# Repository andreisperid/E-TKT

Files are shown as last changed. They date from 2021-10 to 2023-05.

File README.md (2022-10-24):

teaser_4

<br>

<a href="https://certification.oshwa.org/br000010.html" target="_blank">
  <picture>
    <source media="(prefers-color-scheme: dark)" srcset="https://user-images.githubusercontent.com/15098003/196943625-ccef0886-9a68-493c-814a-6e63b238b2bd.png">
    <source media="(prefers-color-scheme: light)" srcset="https://user-images.githubusercontent.com/15098003/196943559-973e30a0-acfd-4a96-a7b8-da4f9bf773d8.png">
    
  </picture>
</a>

<br>

<h1 align="center">E-TKT: anachronic label maker</h1>
<h5 align="center">Andrei Speridião - 2022 - <a href="https://andrei.cc">andrei.cc</a></h6>

<br>

<h3 align="center"><i>An open source label maker that fuses together both old and contemporary technology to create something as ubiquitous as... EMBOSSED LABELS!</i></h2>

<br>

By combining simple and widely available embossing tapes in a reliable mechanism with modern connectivity, E-TKT rescues a *would-be future* that did not happen, and at the same time *gets rid of the dependence on proprietary cartridges*, which are environmentally impacting & expensive.

<br>
<br>

_DSC0933

<br>



<br><br>

# how does it work?

<picture>
  <source media="(prefers-color-scheme: dark)" srcset="https://user-images.githubusercontent.com/15098003/196457261-b6343e3f-528d-4cbe-a548-1b4f4463e4a1.png">
  <source media="(prefers-color-scheme: light)" srcset="https://user-images.githubusercontent.com/15098003/196947337-6aefe414-159e-483b-9dc4-a49cfc82c548.png">
  
</picture>

An *ESP32* commands the label production and also serves an on demand web application (local) to any device connected in a local network.

***Neither internet is needed, nor installing any app.***

<br>

# documentation 

It's now much more detailed, so I've moved it to a [dedicated page](https://andreisperid.github.io/E-TKT/).

### What you fill find there:

- [🎯 news](https://andreisperid.github.io/E-TKT/news.html): what's going on;
- [🤓 about](https://andreisperid.github.io/E-TKT/about.html): how it started, and why?
- [⚙️ how does it work?](https://andreisperid.github.io/E-TKT/how.html): a more in depth explanation;
- [💡 features](https://andreisperid.github.io/E-TKT/features.html): device and app details;
- [📷 gallery](https://andreisperid.github.io/E-TKT/gallery.html): misc. photos of the device and labeled things;
- [🛠️ do it yourself](https://andreisperid.github.io/E-TKT/diy/diy.html): a **super** detailed guide for you to buy the parts and make your own E-TKT;
- [🧬 iterations](https://andreisperid.github.io/E-TKT/iterations/iterations.html): a log of development so far;
- [⚖️ license](https://andreisperid.github.io/E-TKT/license.html): for firmware, hardware and documentation itself;
- [🏅 credits](https://andreisperid.github.io/E-TKT/credits/credits.html): people that made a difference for the project;
- [📺 media](https://andreisperid.github.io/E-TKT/media.html): where and when it's already been featured.

<br>

### If you ever build one, [I would love to know](mailto:hi@andrei.cc) ;)

### And if you'd like, [donations](https://www.paypal.com/donate/?business=U5QYSBT2TLZL8&no_recurring=0&currency_code=USD) are more than welcome 😍

<br>

### *...for other projects: [andrei.cc](https://andrei.cc)*

<br>

_DSC0816

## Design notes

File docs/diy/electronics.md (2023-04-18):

---
layout: default
title: ⚡ electronics
nav_order: 3
description: "E-TKT"
parent: 🛠️ do it yourself!
---

# ⚡ **electronics**

----

💬 *you can find the KiCad v6 source files, PCB 3D export, PDF schematics and gerbers in the [electronic](https://github.com/andreisperid/E-TKT/tree/main/_electronic/) folder.*

----

_DSC0364

----

## Board


----

## Schematics
  
<p align="right">
  <a href="https://github.com/andreisperid/E-TKT/blob/main/_electronic/export/etkt_schematic.pdf" target="_blank">
    <i>🔎 see larger</i>
  </a>
</p>  

----

## Specs
- ***Size:*** 99.6 x 76.2mm(3.92 x 3.00 inches)
- ***Layer count:*** 4
- ***Material:*** FR-4
- ***FR4-TG:*** TG 150-160
- ***Thickness:*** 1.6mm
- ***Min. Track/Spacing:*** 6/6mil
- ***Min. Hole Size:*** 0.3mm↑
- ***Solder Mask:*** Black
- ***Silkscreen:*** White
- ***Surface Finish:*** HASL
- ***Thickness:*** 1.6mm

----

## Subsystems

### Power
  - ***12V*** needs to be provided by an external power supply with at least 3A (real) to deal with servo peaks current while pressing the label. It supplies both the stepper drivers directly.
  - ***6V*** out of the bucket converter and is provided for both the servo and hall sensor. The peak voltage tested on oscilloscope was +1V surge when the servo stalls. *
  - ***3.3V*** is provided by the AZ1117 linear regulator, which receives power directly from the 6V rail.

***Important: Logic level MOSFETs (BSS138)*** were implemented because the ESP32 uses 3.3v logic, we need this conversion for parts that are running on 6V (servo and hall sensor).

<h6><i>* Using a bucket converter for the 6V rail is preferred due to the high step from 12V, but a cheaper alternative using a L7806 (1.5A) is oferred at the PCB back side. For that, you should not mount the bucket converter components (C_POW_IN_1, C_POW_IN_2, C_POW_IN_3, U_POW1, C_POW_BST_1, L1, C_POW_6V_FF1, R_POW_FBT1, R_POW_FFB1, C_POW_OUT_1, C_POW_OUT_2, C_POW_OUT_3, C_POW_OUT_4, C_POW_OUT_5). But IMPORTANT, this exact setup wasn't tested on this exact PCB (only in the preliminar prototype), so do it at your own risk.</i></h6>

### Processing & wireless communication
- Using an ESP32-WROOM-32D-N4, with an integrated antenna.

### Serial USB communication
- An FT231XS-R is used for flashing the firmware through an USB-C 2.0 port.

### Label press
- The MG996-R servo has a maximum constant voltage of 6V. Constant higher tension tends to damage it.

### Character selection (daisy wheel)
- A NEMA stepper driven by a A4988 breakout and a KY 003 hall sensor for homing the daisy wheel.

### Wifi reset
- When this tactile button is pressed while booting the saved wifi credentials are cleared.

### Feeder
- 12v reduced stepper motor (28BYJ-48) driven by a ULN2003 darlington array.

### Graphic user interface
- Running on 3.3v, an I²C OLED display and two DIP LEDs mounted into the J_top piece.

### Buzzer
- Optional magnetic buzzer that plays notes for audible feedback.

----

## Stackup
<p align="center">  

</p>

- **Front (F.Cu)**: most components + mixed signals & power + ground plane;
- **Inner 1 (In1.Cu)**: ground plane;
- **Inner 2 (In2.Cu)**: 6V plane;
- **Back (B.Cu)**: few components + headers + mixed signals and power + ground plane.

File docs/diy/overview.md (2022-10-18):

---
layout: default
title: 🗺️ overview & tips
nav_order: 1
description: "E-TKT"
parent: 🛠️ do it yourself!
---

# 🗺️ **overview & tips**

----

_DSC0414

----

To make your own E-TKT you will need to:
### 1. 3D print
I highly recommend you to have a *3d printer accessible* as you might need to test and tweak the printing settings, since this project demands a certain precision in the fittings;
  
### 2. order a PCB
It's design was oriented to *low cost manufacturing* (4 layers). The two internal layers are ground planes, so it might work with only 2 layers for even lower costs (but it wasn't tested). Don't forget to *order a stencil for the front face* (not needed for the back) together with the PCB.

### 3. buy components
For some electronic parts, you might need to search for alternative *drop-in replacements* (same specs & footprint) as right now there is a general shortage for semiconductors.

### 4. mount the components on the PCB
You can place the components manually in the PCB and then use a home electrical oven/toaster to solder the SMD components. There are PTH headers in the back face and a single SMD electrolytical capacitor that will be easy to deal with a simple soldering station.

### 5. flash the firmware
Very simple process, but please don't forget to *add the data files* together with the firmware.

### 6. assemble the whole package
After making sure the system is working properly, you can proceed to *cable management and physically mounting* the parts together.

### 7. calibrate
The final step makes sure the daisy wheel letters are aligned to the tape and works along with the right pressing force. There is a handy *calibration mode built-in the web app* ;)

<br>

*PS: the PCB order along with the components and it's assembly (steps 2, 3 and 4) might be outsourced by using a turnkey PCB service, but it is funnier to DIY to learn by doing!*

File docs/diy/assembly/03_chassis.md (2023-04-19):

---
layout: default
title: 3. chassis
description: "E-TKT"

parent: 🧩 assembly
grand_parent: 🛠️ do it yourself!
nav_order: 4
---

# **3. chassis**

----

💬 *whenever you need, check out the [exploded view](https://andreisperid.github.io/E-TKT/diy/assembly/assembly.html) for orientation;*

----

This is the foundation of the device. From now on, things will be mounted over it.

_DSC0532

## PCB + NEMA + bottom

_DSC0533
_DSC0534

1. place the PCB and the NEMA assembly together in the A_bottom;
2. pay close attention on the PCB slot on the A_bottom to ease the insertion process;
3. screw 4x m3x20 underneath to attach the NEMA;

## + pillars

_DSC0535
_DSC0536

1. proceeed to use 2x m3x16 screws to hold the pillars, also from the bottom;

## + lateral screws
_DSC0537

1. now, use 3x m3x20 screws from the side to firmly hold the PCB in place

## result
_DSC0538

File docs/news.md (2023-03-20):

---
layout: default
title: 🎯 news
nav_order: 2
description: "E-TKT"
---

# 🎯 **news**

----

### March, 2023
- 🤟 Huge thanks to [Stephen Beechen](https://github.com/sabeechen), who since January has been strongly contributing to the project with great insights and improvements! ([+info](https://github.com/andreisperid/E-TKT/pulls?q=is%3Apr+is%3Aclosed+author%3Asabeechen))

### October, 2022
- Stable PCB, BOM and firmware;
- Documentation with in-depth, step-by-step instructions;

### September, 2022
- ⚠️ A manufactured PCB is being developed and the files are already committed, ***but they are still a work in progress. Aka: not stable and with issues.*** I'm working on that at this moment. Meanwhile, please refer to the [legacy documentation](https://github.com/andreisperid/E-TKT) for reference;

### August, 2022
- E-TKT is a [finalist at the Hackaday Prize 2022, in the Hack it Back category](https://hackaday.com/2022/08/09/2022-hackaday-prize-congratulations-to-the-winners-of-the-hack-it-back-challenge/);
- Huge thanks to [Wesley Lee](https://github.com/wes06) for the assistance on the PCB design and manufacture!

### July, 2022
- Project of the week on [Maker Update #289](https://www.youtube.com/watch?v=3jpaBhROYGc), by [Donald Bell](https://twitter.com/donald);

### June, 2022
- Published the project on [Hackaday](https://hackaday.io/project/185912-e-tkt-anachronic-label-maker)
- E-TKT is now [certified by OSHWA](https://certification.oshwa.org/br000010.html);
- Featured on the front page of [Hackaday](https://hackaday.com/2022/06/15/diy-automated-printer-kerchunks-out-classic-embossed-labels/), [Hackster](https://www.hackster.io/news/e-tkt-prints-embossed-labels-with-the-power-of-iot-5ad25299cf22) and [Make](https://makezine.com/article/maker-news/old-school-label-making-new-school-interface/);

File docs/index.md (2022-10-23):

---
layout: default
title: Home
nav_order: 1
description: "E-TKT"
permalink: /
---
teaser_4

<br>



<h1 align="center">E-TKT: anachronic label maker</h1>

<h6 align="center">Andrei Speridião - 2022 - <a href="https://andrei.cc">andrei.cc</a></h6>

<br>

E-TKT is an open source label maker that fuses together both old and contemporary technology to create something as ubiquitous as... EMBOSSED LABELS!

<br>
<iframe  width="100%" height="500" src="https://www.youtube.com/embed/IKzSupjkA0s" title="YouTube video player" frameborder="0" allow="accelerometer; autoplay; clipboard-write; encrypted-media; gyroscope; picture-in-picture" allowfullscreen></iframe>
<br>

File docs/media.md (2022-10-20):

---
layout: default
title: 📺 media
nav_order: 11
description: "E-TKT"
---

# 📺 **media**

----

### <a href="https://www.youtube.com/watch?v=3jpaBhROYGc" target="_blank">Digi-Key Maker Update</a> (project of the week)
"Ep.289 - Stamp of approval"<br>
*by Donald Bell on June 30, 2022*

----

### <a href="https://makezine.com/article/maker-news/old-school-label-making-new-school-interface/" target="_blank">Make:</a>
"Old School Label Making, New School Interface"<br>
*by Caleb Kraft on June 22, 2022*

----

### <a href="https://www.hackster.io/news/e-tkt-prints-embossed-labels-with-the-power-of-iot-5ad25299cf22" target="_blank">Hacksterio</a>
"E-TKT Prints Embossed Labels with the Power of IoT"<br>
*by Arduino “having11” Guy on June 17, 2022*

----

### <a href="https://hackaday.com/2022/06/15/diy-automated-printer-kerchunks-out-classic-embossed-labels/" target="_blank">Hackaday</a>
"DIY AUTOMATED PRINTER KERCHUNKS OUT CLASSIC EMBOSSED LABELS"<br>
*by Dan Maloney on June 15, 2022*

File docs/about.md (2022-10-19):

---
layout: default
title: 🤓 about
nav_order: 3
description: "E-TKT"
---

# 🤓 **about**

----

## By combining simple and widely available embossing tapes in a reliable mechanism with modern connectivity, E-TKT rescues a ***would-be future that did not happen***, and at the same time reduces the dependence on environmentally impacting DRM-enabled disposable cartridges.

----

## 🧐 **what?**
### *étiquette f (plural étiquettes)*
> ["ticket, memorandum, attach, stick, pierce, sting, to be sharp, goad, puncture, attach, nail"](https://en.wiktionary.org/wiki/%C3%A9tiquette#French)
> 1. tag, label 
> 2. prescribed behavior

It's curious how both meanings are a consequence of each other: we *name things around* to state and reinforce what they are or should be, and at the same time, we end up *influencing our own behaviors* mediated by these labels.

## 🤔 **why?**
### *TLDR: curiosity, technical challenge and of course organizing stuff.*

motex3

The initial spark for this project came from an ordinary manual [labeling device](https://www.aliexpress.com/item/3256801648218535.html) that I bought to organize my workshop. I was ***VERY UPSET*** when I noticed that it was basically rubbish, getting broken and unusable after just a few operations. Just to imagine something made in another part of the world, travelling to me and breaking this way is unbelieavable.

Instead of embossing, it was really embarrassing labels 😅

This little plastic hook (circled in red) grabs a ratchet mechanism (the white plastic part below) to feed the tape forward. I tried to fix and reinforce it, but the failure was unavoidable because there seems to be a critical flaw in the project: it is too weak for the lateral force imposed.

low_DSC8695 copy annotated

At that moment, I could easily buy a brand-new electronic thermal label printer ([such as this Brother model](https://www.brother-usa.com/products/pth110bp)), but something about the vintage embossed finish fascinated me. Also, these new models use expensive DRM [proprietary cartridges](https://www.brother-usa.com/products/tze335) that create a lot of trash after use, not to mention that some other recent models are [DRM protected](https://hackaday.com/2022/03/30/freedmo-gets-rid-of-dymo-label-printer-drm/).

After all, even though the pressing mechanism was poorly made, the daisy wheel was pretty sturdy and sharp-printing. So I thought: can I build over its principles to create a functional device? If so, then why not make it *physical-digital?*

...why bother mixing an archaic printing method with current automation and connectivity features? Because *why not?* It was a technological blind spot ready to be explored!

## 🤯 **reasoning**

### *context & purpose*

1. **CULTURE:** embossed labels are deeply ingrained in culture, as well pointed by [Dan Maloney](https://deadhomersociety.wordpress.com/2015/10/22/quote-of-the-day-2406/) [(*HACKADAY*)](https://hackaday.com/2022/06/15/diy-automated-printer-kerchunks-out-classic-embossed-labels/) and a [spacestationkru](https://best-tv-shows.fandom.com/wiki/Labels_(Dexter%27s_Laboratory)) [(*reddit*)](https://www.reddit.com/r/3Dprinting/comments/vf8acb/comment/icvk1fe/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) and [agent_kater](https://backtothefuture.fandom.com/wiki/Flux_capacitor) [(*reddit*)](https://www.reddit.com/r/3Dprinting/comments/vf8acb/comment/icwgo76/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);
2. **NICHE NEEDS:** there are situations where a paper, flat and/or thermally printed label doesn't fit the needs, let alone the need for the embossed relief;
7. **ERGONOMICS**: when there is no other way than using embossed labels, making them manually is a [straining process](https://www.reddit.com/r/functionalprint/comments/vf8hrq/comment/icvjqvg/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) that might give the operator [repetitive strain injury](https://en.wikipedia.org/wiki/Repetitive_strain_injury);
3. **REACH:** this is a cheap mass-produced device, meaning that lots of [people around the world](https://www.reddit.com/r/coolgithubprojects/comments/vfa2nt/comment/id8e9f5/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) might have one at [home](https://www.reddit.com/r/arduino/comments/vf6rjo/comment/icv9q29/?utm_source=reddit&utm_medium=web2x&context=3) or [work](https://www.reddit.com/r/functionalprint/comments/vf8hrq/comment/icuddop/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);
4. **ENVIRONMENT:** these devices might be already broken: how many kilos of wasted plastic (plus the shipping impact)?
6. **ISSUES:** of course, these folks will be upset and in the end have their needs unaddressed;
8. **ACCESSIBILITY:** [braille labels](https://www.maxiaids.com/reizen-rl-350-braille-labeler) are only a [step of distance](https://www.reddit.com/r/arduino/comments/vf6rjo/comment/icv2cnr/?utm_source=reddit&utm_medium=web2x&context=3) for a possible future [spin off](https://www.reddit.com/r/functionalprint/comments/vf8hrq/comment/icvtlxn/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).

These factors made me think of E-TKT as more than a solution only for myself, but to everyone.

I wanted to create an open source project for a long time and this is why I put a lot of effort into testing all parts extensively and of course crafting this detailed documentation.

## 🤓 **exploration**
###  ...***anachronism***

During the process I've realized that this odd mix between new and old was the biggest underlying curiosity. According to [Wikipedia](https://en.wikipedia.org/wiki/Anachronism):
> “An ***anachronism*** (from the Greek ἀνά ana, 'against' and χρόνος khronos, 'time') is a chronological inconsistency in some arrangements, especially a juxtaposition of people, events, objects, language terms and customs from different time periods”.

The point is: even though the process is digitalized, *the resulting label is totally old school* and there is no easy way of telling if it wasn't made in the traditional way.
  
<br>

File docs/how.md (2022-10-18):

---
layout: default
title: ⚙️ how does it work?
nav_order: 4
description: "E-TKT"
---

# ⚙️ **how does it work?**

----



An *ESP32* commands the label production and also serves an on demand web application (local) to any device connected in a local network.

***Neither internet is needed, nor installing any app.***

### Configuration

The whole process of connecting the E-TKT machine to a local network and then launching the local app is aided by a small ***OLED display*** that provides instructions and a dynamically generated *QR code* with the *URL*, according to the IP attributed by the WLAN.

### Commands

The ***web app*** provides instant text validation, buttons for special characters, a preview of the physical size of the tape, an option to select the desired lateral margins and also real time feedback during the printing process (also present on the device screen). There are specific commands for manually feeding and cutting the tape, and a setup menu where the user can feed a new tape reel and calibrate the machine by adjust the letters alignment and pressure force applied to the daisy wheel.

### Embossing

The label production itself uses the same mechanical principles as the original machine, but is now ***reliable and automated***. A stepper motor feeds the tape while another selects the appropriate character on the daisy wheel according to a home position acquired by a hall sensor. Then a servo motor imprints each character by pressing it's daisy wheel tooth against the tape. That happens successively until the end of the desired label content, when there is a special character position to cut it off. A light blinks to ask for the label to be picked.

----

## Functional block diagram

<br>

<p align="right">
  <a href ="https://user-images.githubusercontent.com/15098003/196293832-6121e267-ee89-4fe7-bddf-c8d8f6bf96c8.png" target="_blank">
    <i>🔎 see larger</i>
  </a>
</p>

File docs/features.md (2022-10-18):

---
layout: default
title: 💡 features
nav_order: 5
description: "E-TKT"
---

# 💡 **features**

----

## 🌟 *highlights*
- No need for internet, app installation, data cables or drivers;
- Command it from any device that is connected to a local network and has a web browser: desktop, tablet, smartphone;
- Compatible with ubiquitous, DRM-less and cheap 9mm generic tape (DYMO-compatible);



## 📱 web app (local)

- Instant preview simulation: what you see is what you get;
- Dynamic check for character validity;
- Estimate of the resulting label dimensions;
- Automatic text centering;
- Margin modes: tight, margin (1 space on each side) or full (maximum input length);
- Buttons for special characters: ♡  ☆  ♪  $ @
- "+ REEL" function to install a new tape reel;
- Manual commands: feed & cut;
- Calibration setup for fine tuning the character alignment and pressing force.

<br>

## 🔌 device

- Full label embossing & cutting;
- Speed: 10 characters per minute;
- Minimum label size to be pickable from the device;
- OLED screen + LED feedback;
- QR code & URL for easily accessing the web app;
- Real time embossing progress;
- Instructions for configuring the wifi;
- Button for clearing the wifi configuration;
- Sound signature: each label owns a subtle melody 🐰🥚

<br>

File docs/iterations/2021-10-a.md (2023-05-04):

---
layout: default
title: 21oct - consist. & usability
nav_order: 96
description: "E-TKT"
parent: 🧬 iterations
---

# **consistency and usability** / Sept-Oct, 2021

----

  

- More compact device, with smaller stepper motor for the daisy wheel.
- Tested using NFC to open web app on smartphone, failed (security standards?).
- OLED display to help on configuration and feedback.
- QR code as an alternative to quickly open web app.
- Improvements on web app usability and visuals.

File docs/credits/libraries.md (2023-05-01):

---
layout: default
title: 📚 libraries
nav_order: 1
description: "E-TKT"
parent: 🏅 credits
---

# 📚 **libraries**

----

### Framework
- Arduino

### Environment
- NODEMCU-32s @3.3.2

### Libraries
- [waspinator/AccelStepper@1.61](https://github.com/waspinator/AccelStepper )
- [madhephaestus/ESP32Servo@0.9.0](https://github.com/madhephaestus/ESP32Servo )
- [ottowinter/ESPAsyncWebServer-esphome@3.0.0](https://github.com/me-no-dev/ESPAsyncWebServer)
- [alanswx/ESPAsyncWiFiManager@0.24](https://github.com/alanswx/ESPAsyncWiFiManager)
- [olikraus/U8g2@2.28.8](https://github.com/olikraus/U8g2)
- [ricmoo/QRCode@0.0.1](https://github.com/ricmoo/QRCode) 
- [bblanchon/ArduinoJson@^6.20.0](https://github.com/bblanchon/ArduinoJson)
- [ayushsharma82/AsyncElegantOTA@2.2.5 ](https://github.com/ayushsharma82/AsyncElegantOTA)

A big thank you for the library developers!

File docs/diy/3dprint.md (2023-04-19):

---
layout: default
title: 🧵 3D printing
nav_order: 2
description: "E-TKT"
parent: 🛠️ do it yourself!
---

# 🧵 **3D printing**

----

💬 *you can find both the STL and source files in the [3d_print](https://github.com/andreisperid/E-TKT/tree/main/_3dprint) folder.*

----

_DSC0212

----

### 16 parts in total, using approximately 220g of filament (I've used PETG).

----

<div class="sketchfab-embed-wrapper"> 
 <iframe title="E-TKT: 3D printing" width="100%" height="600px" frameborder="0" allowfullscreen mozallowfullscreen="true" webkitallowfullscreen="true" allow="autoplay; fullscreen; xr-spatial-tracking" xr-spatial-tracking execution-while-out-of-viewport execution-while-not-rendered web-share src="https://sketchfab.com/models/af2f40abf97d477f9c3f3be6128178a7/embed?autostart=1"> </iframe> 
</div>

### 📐 All the [.stl provided](https://github.com/andreisperid/E-TKT/tree/main/_3dprint/stl) are in the correct orientation for optimal printing:

- A_bottom \*
- B_wall \*
- C_wall_track \*
- D_pillar
- E_pillar
- F_pillar
- G_pillar
- H_nema_cover \*
- I_nema_wheel_hub
- J_top \*
- K_top_screenholder
- L_top_tapefeeder
- M_top_wheel_cover
- N_wheel_coupling_bottom
- O_wheel_coupling_top
- P_press
 
***\* needs support***

### 🎛️ Recommended settings
- Layer height: 0.20mm
- Infill: 20%
- Wall line count: 3 + 1 (alternating extra wall with Cura)
- Top/bottom layers: 5

PS: [here](https://github.com/andreisperid/E-TKT/tree/main/_3dprint/source) you can find the source 3D files (STEP).

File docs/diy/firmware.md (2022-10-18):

---
layout: default
title: 💻 firmware
nav_order: 5
description: "E-TKT"
parent: 🛠️ do it yourself!
---

# 💻 **firmware**

----

💬 *if you want to know more about the code, please check the [firmware](https://github.com/andreisperid/E-TKT/blob/main/src/LabelMaker.cpp) and the [app scripts](https://github.com/andreisperid/E-TKT/blob/main/data/script.js)*.

----

_DSC0743

----

1. Clone the [repository](https://github.com/andreisperid/E-TKT);
2. Make sure you have the [framework and all the libraries](https://andreisperid.github.io/E-TKT/credits/libraries.html) installed on your computer (I use [Visual Studio Code](https://code.visualstudio.com/) with [PlatformIO](https://platformio.org/) and recommend it!);
3. Flash the code into the PCB using an USB-C cable \*;
4. Upload the files ("data" folder) to the ESP32 using SPIFFS \*.

*\* don't forget to hold the \*FN button to enter DFU mode*

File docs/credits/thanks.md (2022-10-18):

---
layout: default
title: 🙂 thanks
nav_order: 3
description: "E-TKT"
parent: 🏅 credits
---

# 🙂 **thanks**

----

### Especially to
- **[Ana Marini](https://anamarini.com/):** for the initial idea of having embossed labels, which started all the process (and the motivation all along);
- **José Speridião Junior:** for several insights that improved the printing mechanics, leading to better labels;
- **[Wesley Lee](https://wes.am):** for the assistance on the PCB design, manufacture and assembly;

& the authors of the [libraries](https://andreisperid.github.io/E-TKT/credits/libraries.html) used,

& to [Michael Tension](http://www.tensiontype.com), author of the [Impact Label](https://www.dafont.com/impact-label.font) font,

& the authors of 3D models used throughout the process:
- [LED TFT 0.96 inch 64x128 by Mih Kov](https://grabcad.com/library/oled-tft-0-96-inch-64x128-monochrome-i2c-1);
- [28BYJ-48 - 5V by Pablo Galarce](https://grabcad.com/library/stepper-motor-28byj-48-5v-dc-1);
- [ULN2003 by Aron Rubin](https://grabcad.com/library/uln2003-unipolar-stepper-driver-board-1);
- [MG-995 by Hasanain Shuja](https://grabcad.com/library/hobby-servo-motors-for-rc-cars-planes-etc-1);

& last but not least, to everyone that contributed with constructive criticism and cool ideas!

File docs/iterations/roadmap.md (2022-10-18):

---
layout: default
title: 🚀 roadmap
nav_order: 1
description: "E-TKT"
parent: 🧬 iterations
---

# 🚀 **roadmap**

----

## [🐛 bugfix](https://github.com/andreisperid/E-TKT/issues?q=is%3Aopen+is%3Aissue+label%3Abug)

----

## features
### 📌 planned
- ~~manufactured PCB~~
- ~~documentation~~
- ~~letter calibration~~

### 🎈 nice to have
- adjustable kerning
- adaptive kerning
- random kerning
- custom daisy wheels

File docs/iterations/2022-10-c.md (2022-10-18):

---
layout: default
title: 22oct - calibration setup
nav_order: 88
description: "E-TKT"
parent: 🧬 iterations
---

# **calibration setup** / October, 2022   

----

The embossing process has been undoubtedly the most challenging part of the project, so I wanted to make sure that anyone making their own E-TKT would not struggle as I did.

These are the most critical steps:
1. the targeted daisy wheel tooth must be perpendicular to the tape;
2. the press head must be aligned to the middle of that tooth;
3. the pressing needs to happen with the right force;



----

## Now for the involved components:

### Hall sensor



Depending on the hall's lateral position, the rotating magnet might activate the sensor earlier or later, impacting lateral character alignment.

The main issue that happens with that misalignment is the *skewed / italic* aspect for the character, because the letter is not pressed when perpendicular to the tape (remember it is a rotating wheel). This is the first issue that must be solved.



⚠️ It will be highlighted on the instructions the need to make sure the hall is as centered as possible visually before moving on the assembly.

### Servo & Press (3D printed):



There are three factors into the equation:
- the part's intrinsic imprecision (especially on cheap servos);
- the assembly position of the servo itself on the structure;
- the coupling of 3d printed part that does the pressing job into the servo might affect the angle, and for that I have changed the parts design to help with that alignment.

Also, depending on the servo used, the distance from the servo to the daisy wheel tooth might change. I'm providing different models that can be experimented to address that. Or, since the STEP files are open, anyone can modify it to match their needs.

----

## Calibration Process

In general, all factors above can make the letters vanish on their sides.



For addressing that (and the skewed / italic effect), I have created a calibration procedure that have two main moments:

### 1 - During assembly / firmware, where the parts' rough imprecisions are to be visually adjusted (without wasting tape).

Both `assemblyCalibrationAlign` and `assemblyCalibrationForce` are hardcoded variables that make sure there is a good starting point for further tuning.

The standard values are working on a cheap MG996-R servo (I'm pretty sure mine is a ripoff).

### 2 - After assembly, by testing with the actual embossed label with more precise adjusts.

The fine tuning is possible thanks to the SETUP menu in the web app. It is very frustrating adjusting values every time by code and flashing and that's why I though about that easily accessed screen.



***Alignment + test (light):*** it's possible to choose a value between 1 and 9 (5 is the default neutral). By picking a number, there is a test button on the right that when pressed, starts a routine that reaches to the letter "M" (widest character available) and very slowly moves the press towards the tooth until it lightly touches it. It is possible to check if the press is aligned when hitting the tooth.

***Force + test (full):*** this parameter controls how much the servo will press the tooth against the tape, and of course, the tape should be already reeled. Again, values from 1 to 9, but this time 1 is the default, lighter pressure. To test, there is a big test button on the right that will end up testing both the force and alignment.


*(force tests, from 1 to 9)*

***Cancel:*** if there was any unsaved changes it will pop up a warning, otherwise it goes back to the main screen.

***Save:*** by hitting save, the machine will save the values in memory then reboot and the app will automatically refresh in 15 seconds.

*PS: the "+ reel" button has been brought from the main screen.*

## ready to label? 😀

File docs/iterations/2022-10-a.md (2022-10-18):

---
layout: default
title: 22oct - device GUI
nav_order: 90
description: "E-TKT"
parent: 🧬 iterations
---

# **device GUI** / October, 2022   

----

The previous OLED display was really cute for its small 128x32px size, but it wasn't working well for the QR code. 

Imagine a square with less than 10x10mm, shinning bright (OLED). It was really hard to focus with the smartphone camera.

I've then decided to switch for a similar but bigger I2C OLED display, now with 128x64px:

_DSC9705

Then I've took advantage of its taller real state to improve and/or implement new screens:

- **splash:** more about that soon, with an nerdy extra feature;
- **wi-fi reset**;
- **wi-fi setup:** cold start or after reset;
- **E-TKT ready state:** QR code + text of the local assigned IP to access the web app;
- **printing progress**;
- **printing finished**;
- **cutting, feeding and reeling:** requested manually from the web app);
- **saving settings:** more about that in the following updates;
- **rebooting;**

It turns out that having not so many pixels to push around is pretty funny. Also, I've used symbols with a dedicated font to improve the meaning and communication.

Thanks to olikraus for the amazing U8g2 library that is super useful.

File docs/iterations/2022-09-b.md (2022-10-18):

---
layout: default
title: 22sep - improved structure
nav_order: 91
description: "E-TKT"
parent: 🧬 iterations
---

# **improved structure** / September, 2022

----

Since the beginning of the month I've been exhaustively testing and improving the 3D printed structure and now it is working nicely together with the manufactured PCB. The overall shape is now a little bit rounder, still not final though!

Major changes:
- **Hall sensor:** the new support for the breakout hall sensor is now provided by the pillar, making it easier to attach as the PCB is attached to it (and taking advantage of the 3 pin 2.54mm female header on the PCB);
- **PCB:** is locked tightly on both surrounding pillars and 6 screws and helps the overall rigidity;
- **Daisy wheel:** attending several feedbacks (including from [David Knochenhauer](https://hackaday.io/Knochi), thank you!), I've made it removable and as a bonus, the initial assembly process is now much easier!
- **Feeder:** its new design takes advantage of the PETG's own flexibility, removing one pesky item from the B.O.M., the spring;
- **Display:** the bigger OLED with 128x64 pixels made the QR code totally straightforward to read (was pretty hard to focus) and also the overall GUI reading is much better (more updates on the GUI soon);
- **Press:** with this new shape the initial alignment when assembling is easier now, and its structural rigidity is greatly improved too. Also, it uses a M6 washer in contact with the servo to make sure it doesn't bend when pressed, while at the same time allowing it to rotate freely.

_DSC9659
_DSC9663
_DSC9664
_DSC9667
_DSC9673
_DSC9669
_DSC9670

Some photos of the printing process, aiming for that sharp first layer.
_DSC9260
_DSC9334

PS: the revised v1.0 PCB with several adjusts has already shipped, more about that soon!

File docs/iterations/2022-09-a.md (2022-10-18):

---
layout: default
title: 22sep - PCB v0.9 assembly
nav_order: 92
description: "E-TKT"
parent: 🧬 iterations
---

# **PCB v0.9 assembly** / September, 2022

----

My first PCB ever is the E-TKT's alpha version.

I've been thinking of that moment for a decade and I am pretty happy with the result! Thanks again for Wes for providing the manufacture and components' order in one of his batches. He even assisted me on assembling and baking the board at his place.

_DSC8825
_DSC8806
_DSC8788

Now for the list of fixes for v1.0:
- I've mistakenly switched the Reset and Flash button position/labels;
- The latch power circuit didn't work, so I will be changing it to a compact SMD switch + MOSFET;
- Remove 3V3 from the FTDI;
- Several LEDs are logically inverted (on when they should be off): hall, servo, a4988 enable signals;
- Some LED brightness are too high;
- The manufacturer put the "E-TKT" letters on white silk, when it should be in black solder mask. In the end, I've liked it better, so I will consider  to incorporate this happy accident on the project;
- Insert OSHWA label & certification;
- Invert RX/TX silk arrows on FTDI LEDs.
- Apart from these minor issues, the circuit has been working great and soon there will be more work in progress. Right now I'm working on the improved 3d printed parts with new features, together with the web app.

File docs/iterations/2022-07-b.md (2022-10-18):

---
layout: default
title: 22jul - PCB version 0.9
nav_order: 93
description: "E-TKT"
parent: 🧬 iterations
---

# **PCB version 0.9** / July, 2022

----

First of all, I'd like to start by saying a big thank you to [Wesley Lee](https://github.com/wes06), an inspiring old friend of mine that gave me a lot of tips, suggestions and lessons about PCB design.

0 9_3d_front
0 9_3d_back

Among several improvements, these were the major changes for this 0.9 version that already went into production:

- **Bucket 6V regulato:** Wes suggested using it instead of a linear regulator (big drop from 12V to 6V), and why not? I've ended up learning a little bit about EMI;
- **Latch power switch:** Wes also suggested that by sending me this reference from Dave's EEV Blog. Initially I was looking to use a MOSFET + small slide switch, but being able to use the same tact button as the other commands for that was a nice idea.
- **Visual identity:** in a serendipitous coincidence I've found the superposition of routing tracks+ vias + the real scale "E-TKT" logo a great sum of what "anachronical" is. And this is all about a designer doing a PCB: I bent a little bit the best routes just for making it conceptual. We'll need to see the readability between the solder mask + FR4 + ENIG, but I think it will be alright. Also, I've done custom graphics for the commands, inspired by teenage engineering (I'll get there one day...).
- **Improved edge cuts:** thanks again to Wes, now with proper achievable fillets and mouse bites;
- **Buzzer:** because why not? Maybe simple quick tones as feedbacks;
- **Hierarchical sheets:** not exactly on the PCB itself, but I've loved organizing the subsystems in modules, easing its reutilization.

0 9_front
0 9_back

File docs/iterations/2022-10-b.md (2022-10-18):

---
layout: default
title: 22oct - design inspo. & UI
nav_order: 89
description: "E-TKT"
parent: 🧬 iterations
---

# **design inspiration & UI** / October, 2022   

----

### *If you just want to see the final UI design for the app in detail, please [scroll all way down](https://andreisperid.github.io/E-TKT/iterations/2022-10-b.html#wait-a-minute-but-what-about-e-tkts-ui)* ;)



### 🍷 Now for a conceptual and reflective update to discuss a bit about design...

First, remember that E-TKT is all about anachronism, which means it aims on manipulating the order things logically have/are occurring in an unusual way while presenting something odd but logically plausible. Think of "what could have happened if ______?"

Expanding that further on, I wanted to incorporate that approach into the digital interface accessed through the smartphone.

## Physical informs the digital

Green characters on black, dull gray boxes, overwhelming gradients, shinny reflective icons and long shadows over colorful flat interface elements were some of the visual design trends we've been interacting with for the past 50 years (well, not all that time in my case :P ).

But there is a theme that resurfaces from time to time: [skeuomorphism](https://en.wikipedia.org/wiki/Skeuomorph), which in a nutshell is the idea of emulating  characteristics of original artifacts as ornaments in derivative ones. A well-known example is [Apple iCal (calendar)](https://arstechnica.com/gadgets/2011/07/mac-os-x-10-7/5/), which had leather textures in its interface to create familiarity with the traditional physical calendar that used that material for functional and aesthetic reasons.

<p align="right">
<i>source: Ars Technica</i></p>

Dieter Rams, an industrial designer best known for his Braun creations, had a [great influence on Apple products](https://theultralinx.com/2014/03/dieter-rams-inspired-apple-products/), both physical and digital. That includes the ET66 calculator that inspired Apple's software version that came together with Mac OSX.

## What should we keep?

When looking to the E-TKT device and more specifically its daisy wheel, I've got some "typewriter" vibes from it. And, there is no doubt that Olivetti came to mind as one of the major Italian design symbols of the XX century. My parents still have an 80s electric typewriter from the brand.

I've then remembered my industrial design classes when I first knew about [Divisumma 18](https://www.moma.org/collection/works/3805) and its simple and monolithic yellow aspect. It was designed by Mario Bellini in 1972.

<p align="right">
<i>source: MoMA</i></p>

Apart from its great shape that was very contrasting to the bulky machines at the time, perhaps the most attractive characteristic is on the buttons that almost ***BEG to be pressed***. That was well though by Bellini, that based it on anthropomorphic concepts, which means attributing human characteristics to non-human things.

The boundaries of our body are made of skin-covered meat. What is our touch to be sensibilized and actuated back with?

Well, displays are hard to the touch, but nowadays we can cheaply "borrow the screen" for things that are not critical, thus having a world of possibilities by using visual, audible and/or haptic cues to emulate the juicy physical stuff.

PS: as an "accidental" phylosophical loophole, [Olivetti was(is) based in *Ivrea*, Italy](https://www.nytimes.com/2019/08/28/t-magazine/olivetti-typewriters-ivrea-italy.html). Yes, the same place where *Arduino* got born many decades later.

### ...anachronism as tool for finding atemporal loopholes! 🤓

## ...wait a minute, but what about E-TKT's UI?
All of that to say that I have reached a final version for the user interface for the web app by extracting the essence of the concepts discussed above.

The color pallete is now following a blue-yellowish duet. The buttons were rounded and for the color-coded functions, there is a light halo that glows when pressed.

A new addition is the setup screen, which I will talk a bit more in another update.



The soft pressing and illumination effects were both achieved by using pure CSS & Javascript to minimize the data storage and transfer.



📱

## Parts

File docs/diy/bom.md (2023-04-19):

---
layout: default
title: 📝 bill of materials
nav_order: 4
description: "E-TKT"
parent: 🛠️ do it yourself!
---

# 📝 **bill of materials**

----

_DSC0022

----

## 💬 cost per unit

The estimated cost for the components (without attrition) is around **$100 (USD) without shipping and taxes**, as of October 2022.

This value takes into account all the breaking points for a single E-TKT device and includes the manufacturing of 5 PCBs (4 layers) plus a stencil for the front layer.

----

## A. structure & mechanic 

| TYPE | SPEC | REF | QTY |
| :--- | :--- | :---: | :---: |
| 3D print | filament — PETG | [link](http://prusa3d.com/product/prusament-petg-jet-black-1kg/) | ~220g |
| socket head screw | ISO 4762 - M3 x 40 - A2-70 | [link](http://aliexpress.com/item/2261799963738734.html) | 1 |
| socket head screw | ISO 4762 - M3 x 20 - A2-70 | [link](http://aliexpress.com/item/2261799963738734.html) | 18 |
| socket head screw | ISO 4762 - M3 x 16 - A2-70 | [link](http://aliexpress.com/item/2261799963738734.html) | 7 |
| socket head screw | ISO 4762 - M3 x 10 - A2-70 | [link](http://aliexpress.com/item/2261799963738734.html) | 4 |
| socket head screw | ISO 4762 - M3 x 8 - A2-70 | [link](http://aliexpress.com/item/2261799963738734.html) | 2 | 
| socket head screw | ISO 4762 - M3 x 6 - A2-70 | [link](http://aliexpress.com/item/2261799963738734.html) | 9 | 
| socket head screw | ISO 4762 - M4 x 10 - A2-70 | [link](http://aliexpress.com/item/2261799963738734.html) | 1 | 
| hex nut | DIN EN ISO 4032 - M3 - A2-70 | [link](http://aliexpress.com/item/1005001966426139.html) | 10 | 
| washer | DIN EN ISO 7090 - 3 - 200 HV - A2 | [link](https://aliexpress.com/item/1005003991819416.html) | 9 | 
| washer | DIN EN ISO 7090 - 6 - 200 HV - A2 | [link](https://aliexpress.com/item/1005003991819416.html) | 1 | 
| silicone pad feet | ⌀8x2mm | [link](http://aliexpress.com/item/2251832637568894.html) | 4 | 
| daisy wheel | MOTEX — uppercase, 43 chars. |  [link](https://www.aliexpress.com/item/1005004489017299.html) | 1 | 
| deep groove ball bearing | 608-2Z | [link](https://www.aliexpress.com/w/wholesale-608%2525252d2z-bearing.html) | 1 | 
| deep groove ball bearing | 623-2Z | [link](https://www.aliexpress.com/w/wholesale-623%2525252d2z-bearing.html) | 2 | 
| extruder gear | MK8 40 teeth / 5mm axis | [link](http://aliexpress.com/item/2255800252771556.html) | 1 |

----
 
## B. sensors & actuators

| TYPE | SPEC | REF | QTY |
| :--- | :--- | :---: | :---: |
| hall sensor (breakout) | Keyes KY 003 | [link](http://aliexpress.com/item/2251832475321023.html) | 1 | 
| stepper driver (breakout) | A4988 | [link](http://aliexpress.com/item/3256801435362018.html) | 1 |
| stepper motor | NEMA 17HS4023 + cable | [link](http://aliexpress.com/item/2251832620474591.html) | 1 |
| stepper motor | 28BYJ-48 12V | [link](https://www.aliexpress.com/item/1005003708064424.html) | 1 | 
| servo | Towerpro MG-996R | [link](http://aliexpress.com/w/wholesale-Towerpro-MG%2525252d996R.html) | 1 | 
| neodymium magnet | ⌀2mm x 3mm length | [link](https://aliexpress.com/item/1005003022293200.html) | 1 |
| LED | Clear white —	DIP 2x5x7mm | [link](https://www.aliexpress.com/item/1005003347290499.html) | 1 |
| OLED display | SSD1306, 128x64, monochrome white — 4 pin I²C | [link](https://www.aliexpress.com/item/1005003484018034.html) | 1 |

----

## C. PCB & components

| TYPE | SPEC — PACKAGE | REF | QTY |
| :--- | :--- | :---: | :---: |
| PCB | 4 layers, FR4, black solder mask — 99.57 mm x 76.2 mm | | 1 |
| stencil | top layer only (F.Cu) — 200mm x 150mm | | 1 |
| MCU | ESP32 — WROOM-32D (SMD) | [ESP32-WROOM-32D-N4](https://www.findchips.com/search/ESP32-WROOM-32D-N4) | 1 |
| serial | USB Interface, Full Serial UART — SSOP-20 3.9x8.7mm (SMD) | [FT231XS-R](https://www.findchips.com/search/FT231XS-R) | 1 |
| driver | Darlington 50v 500mA — SOIC-16 3.9x9.9mm (SMD) | [ULN2003ADRE4](https://www.findchips.com/search/ULN2003ADRE4) | 1 |
| regulator | Switching, 4.5-28V 3A Output — SOT-23-6 (SMD) | [TPS54302](https://www.findchips.com/search/TPS54302) | 1 |
| regulator | LDO 3.3V 800mA — SOT-223 (SMD) | [AZ1117CH-3.3TRG1](https://www.findchips.com/search/AZ1117CH-3.3TRG1) | 1 |
| TVS diode | USB6B1 — SOIC-8 3.9x4.9mm (SMD) | [USB6B1RL](https://www.findchips.com/search/USB6B1RL) | 1 |
| inductor | 10uH 20% 7A — SRP6060 (SMD) | [SRP6060FA-100M](https://www.findchips.com/search/SRP6060FA-100M) | 1 |
| buzzer | Electromagnetic 3V — CSS-0575A (SMD) | [CSS-0575A-SMT](https://www.findchips.com/search/CSS-0575A-SMT) | 1 |
| MOSFET | N-CH 0.22A, 50V, 1.5V — SOT-23 (SMD) | [BSS138LT3G](https://www.findchips.com/search/BSS138LT3G) | 2 |
| BJT | 625mW, 25V, 1.5A — SOT-23 (SMD) | [MMSS8050-L-TP](https://www.findchips.com/search/MMSS8050-L-TP) | 2 |
| button | OFF-(ON) — 6X6X3.1mm (SMD) | [B3FS-1000](https://www.findchips.com/search/B3FS-1000) | 3 |
| ferrite | 40 Ohms 5A — 0805 (SMD) | [MH2029-400Y](https://www.findchips.com/search/MH2029-400Y) | 1 |
| fuse | 6V 750mA — 0805 (SMD) | [0ZCK0075FF2E](https://www.findchips.com/search/0ZCK0075FF2E) | 1 |
| LED | LED white — 0603 (SMD) | [SMLD12WBN1W1](https://www.findchips.com/search/SMLD12WBN1W1) | 12 |
| capacitor | Electrolytical 100uF 25V — 6.3x7.7 (SMD) | [EMVE250ADA101MF80G](https://www.findchips.com/search/EMVE250ADA101MF80G) | 1 |
| capacitor | Ceramic 22uF 25V X7R — 1210 (SMD) | [C3225X7R1E226M250AB](https://www.findchips.com/search/C3225X7R1E226M250AB) | 8 |
| capacitor | Ceramic 10uF 12V X7R — 0603 (SMD) | [GRM188Z71A106KA73D](https://www.findchips.com/search/GRM188Z71A106KA73D) | 6 |
| capacitor | Ceramic 0.1uF 50V X7R — 0603 (SMD) | [C1608X7R1H104K080AA](https://www.findchips.com/search/C1608X7R1H104K080AA) | 6 |
| capacitor | Ceramic 47pF 5V X7R — 0603 (SMD) | [CGA3E2C0G1H470J080AA](https://www.findchips.com/search/CGA3E2C0G1H470J080AA) | 3 |
| resistor | Thick Film 100K — 0603 (SMD) | [ERJ-3EKF1003V](https://www.findchips.com/search/ERJ-3EKF1003V) | 1 |
| resistor | Thick Film 11K — 0603 (SMD) | [ERJ-3EKF1102V](https://www.findchips.com/search/ERJ-3EKF1102V) | 1 |
| resistor | Thick Film 10K — 0603 (SMD) | [ERJ-3EKF1002V](https://www.findchips.com/search/ERJ-3EKF1002V) | 9 |
| resistor | Thick Film 5K1 — 0603 (SMD) | [ERJ-3EKF5101V](https://www.findchips.com/search/ERJ-3EKF5101V) | 7 |
| resistor | Thick Film 2K — 0603 (SMD) | [ERJ-3EKF2001V](https://www.findchips.com/search/ERJ-3EKF2001V) | 1 |
| resistor | Thick Film 100R — 0603 (SMD) | [ERJ-3EKF1000V](https://www.findchips.com/search/ERJ-3EKF1000V) | 6 |
| resistor | Thick Film 27R — 0603 (SMD) | [ERJ-3EKF27R0V](https://www.findchips.com/search/ERJ-3EKF27R0V) | 4 |
| connector | USB-C 2.0 — GCT USB4105-GF-A | [GCT USB4105-GF-A](https://www.findchips.com/search/USB4105-GF-A) | 1 |
| connector | Barrel Jack 2mm/6.3mm, 5A 20V — DCJ200 | [DCJ200-10-A-K1-K](https://www.findchips.com/search/DCJ200-10-A-K1-K) | 1 |
| connector | Conn_01x02_Male — Header 1x02 P2.54mm Vertical | [M20-9990245](https://www.findchips.com/search/M20-9990245) | 2 |
| connector | Conn_01x03_Male — Header 1x03 P2.54mm Vertical | [M20-9990346](https://www.findchips.com/search/M20-9990346) | 2 |
| connector | Conn_01x04_Male — Header 1x04 P2.54mm Vertical | [M20-9770446](https://www.findchips.com/search/M20-9770446) | 1 |
| connector |Conn_01x05_Male — Header 1x05 P2.54mm Vertical | [M20-9990546](https://www.findchips.com/search/M20-9990546) | 1 |
| connector | Conn_01x04_Male — Header 1x04 P2.54mm Horizontal | [M20-9750446](https://www.findchips.com/search/M20-9750446) | 1 |
| connector | Conn_02x08_Female — Socket 2x08 P2.54mm Vertical (A4988) | [M20-7820842](https://www.findchips.com/search/M20-7820842) | 2 |

### \* *Alternative 6V power*

| TYPE | SPEC — PACKAGE | REF | QTY |
| :--- | :--- | :---: | :---: |
| capacitor | Ceramic 0.33uF 50V X7R — 0603 (SMD) | [CGA3E3X7R1H334M080AB](https://www.findchips.com/search/CGA3E3X7R1H334M080AB) | 1 |
| capacitor | Ceramic 0.1uF 50V X7R — 0603 (SMD) | [C1608X7R1H104K080AA](https://www.findchips.com/search/C1608X7R1H104K080AA) | 1 |
| regulator | Linear 6v 1.5A — TO-220 | [L7806CV](https://www.findchips.com/search/L7806CV) | 1 |

----

## D. harnesses

| TYPE | SPEC | REF | QTY |
| :--- | :--- | :---: | :---: |
| cable | USB A to C data cable (firmware flash only) | | 1 |
| wiring | flat, flexible | [link](http://aliexpress.com/item/2251832639497810.html) | 1 |
| connector | female - 1x02 P2.54mm dupont | [link](http://aliexpress.com/item/3256802073547679.html) | 2 |
| connector | female - 1x04 P2.54mm dupont | [link](http://aliexpress.com/item/3256802073547679.html) | 2 |

----

## E. other

| TYPE | SPEC | REF | QTY |
| :--- | :--- | :---: | :---: |
| power | 12V 3A (real) 5,5mm x 2,1mm barrel jack, center positive | [link](https://aliexpress.com/item/1005002620565526.html) | 1 |
| label tape | 9mm DYMO-compatible | [link](https://www.aliexpress.com/item/1005002288190756.html) | 🦝 |

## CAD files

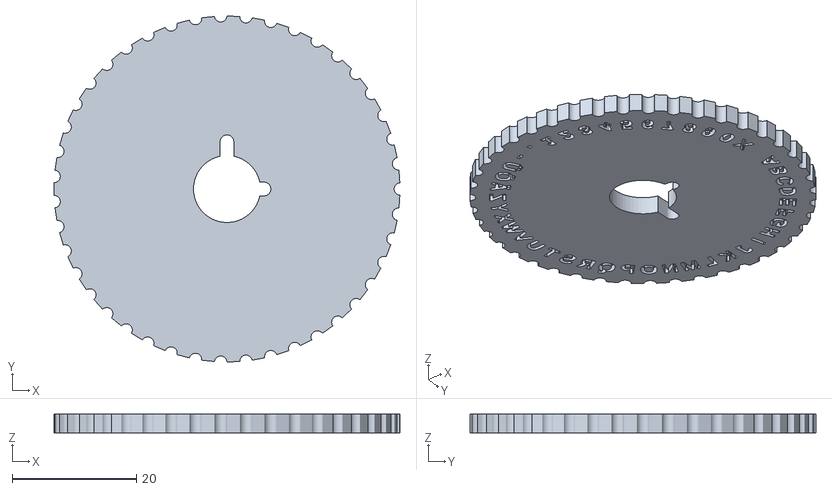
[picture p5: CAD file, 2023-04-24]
_3dprint/customPressWheels/STL/pressWheel_42_ABC123_test_Top.stl
55.8 x 55.8 x 3.00

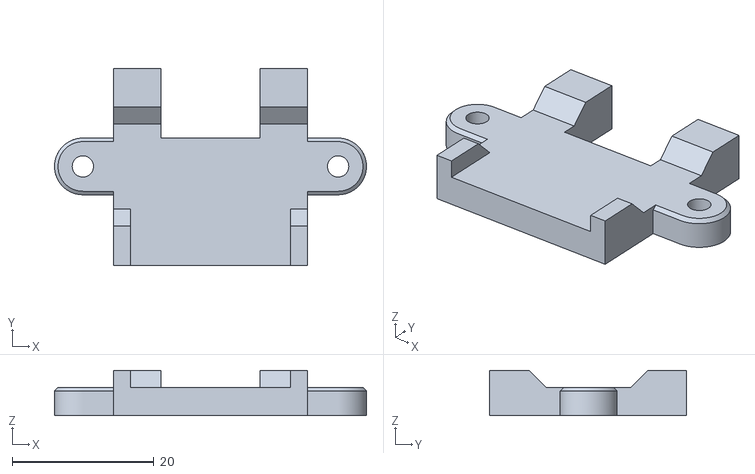
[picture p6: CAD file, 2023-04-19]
_3dprint/stl/K_top_screenholder.stl
44.0 x 27.8 x 6.40

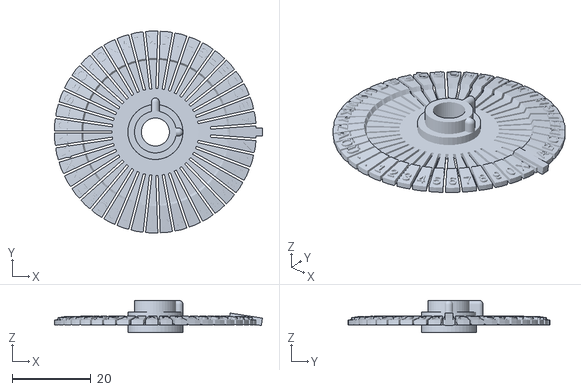
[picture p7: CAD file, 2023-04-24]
_3dprint/customPressWheels/STL/pressWheel_42_ABC123_test.stl
52.7 x 51.3 x 8.20

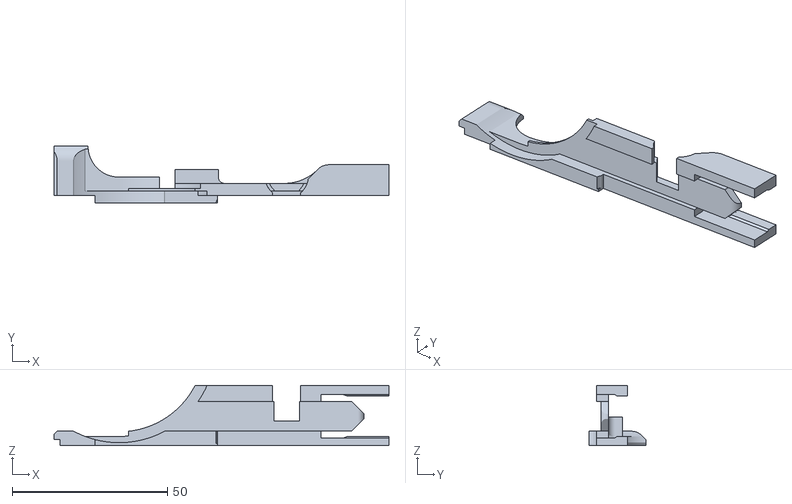
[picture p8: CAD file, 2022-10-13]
_3dprint/stl/C_wall_track.stl
108.0 x 18.3 x 19.5

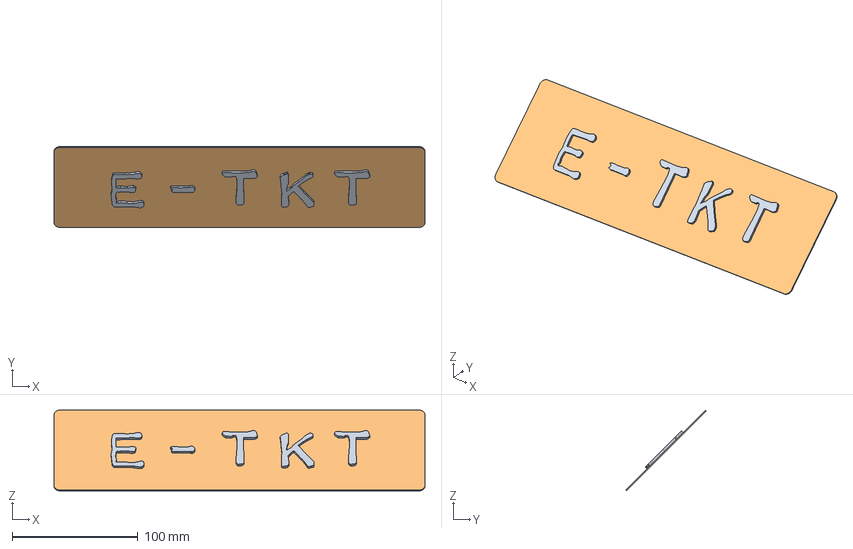
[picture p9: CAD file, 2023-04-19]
_3dprint/source/E-TKT_025-logo_E-TKT.stp
295.1 x 64.3 x 64.3 mm

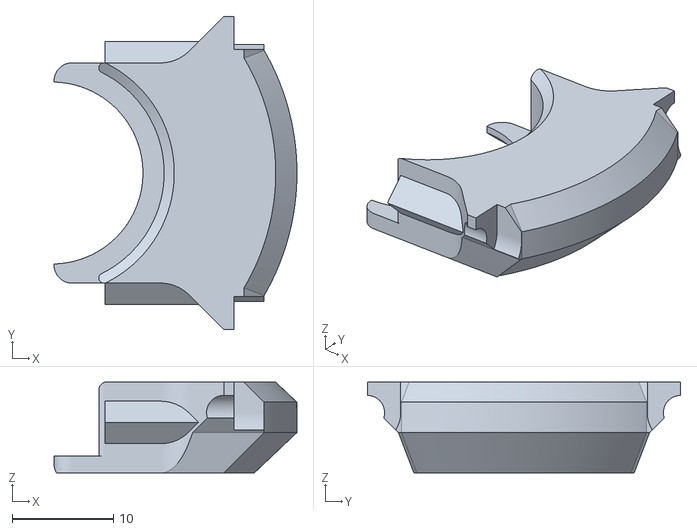
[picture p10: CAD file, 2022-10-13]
_3dprint/stl/M_top_wheel_cover.stl
24.0 x 31.0 x 9.00

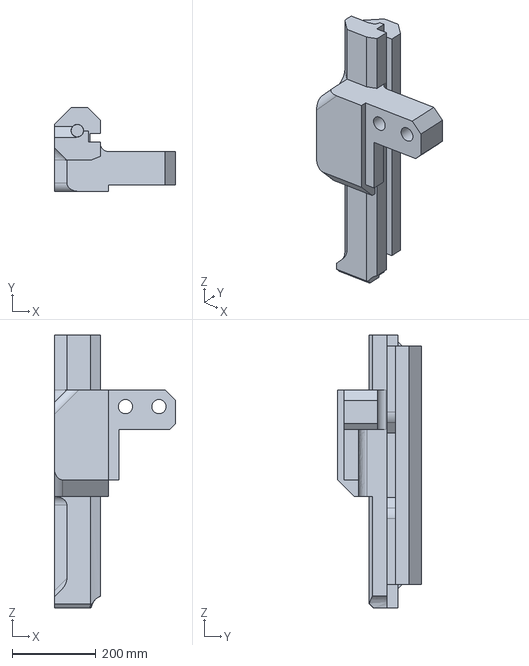
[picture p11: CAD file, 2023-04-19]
_3dprint/source/E-TKT_025-structure_F_pillar.stp
290.0 x 200.0 x 652.0 mm

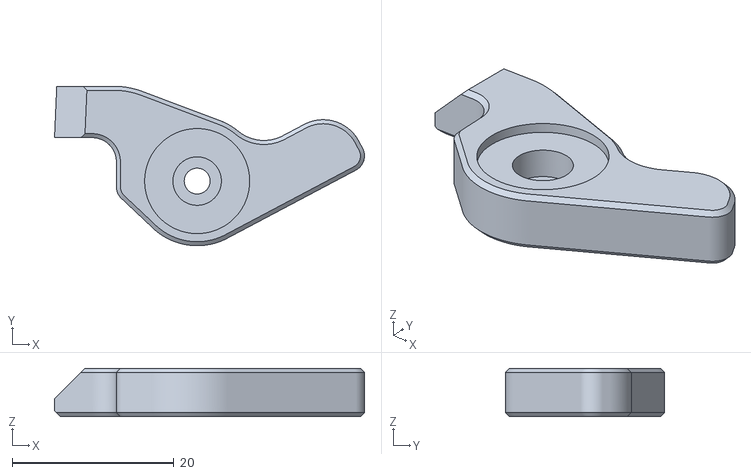
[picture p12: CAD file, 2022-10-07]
_3dprint/stl/P_press_1mmleft.stl
38.4 x 19.7 x 6.00

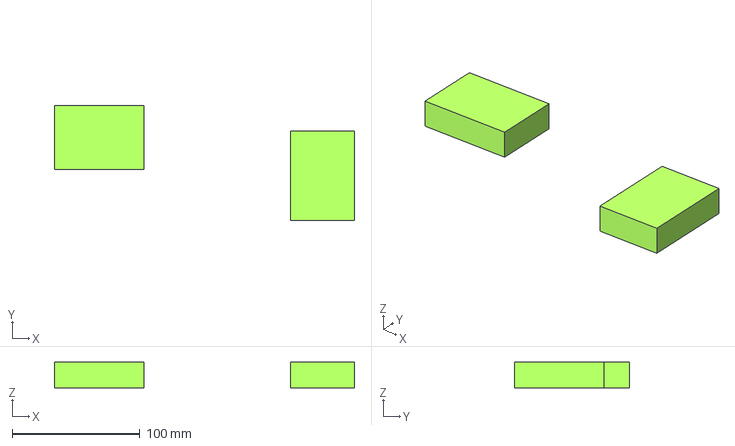
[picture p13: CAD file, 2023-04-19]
_3dprint/source/E-TKT_025-electronic_LED_DIP-2x5x7mm.stp
235.0 x 90.0 x 20.0 mm

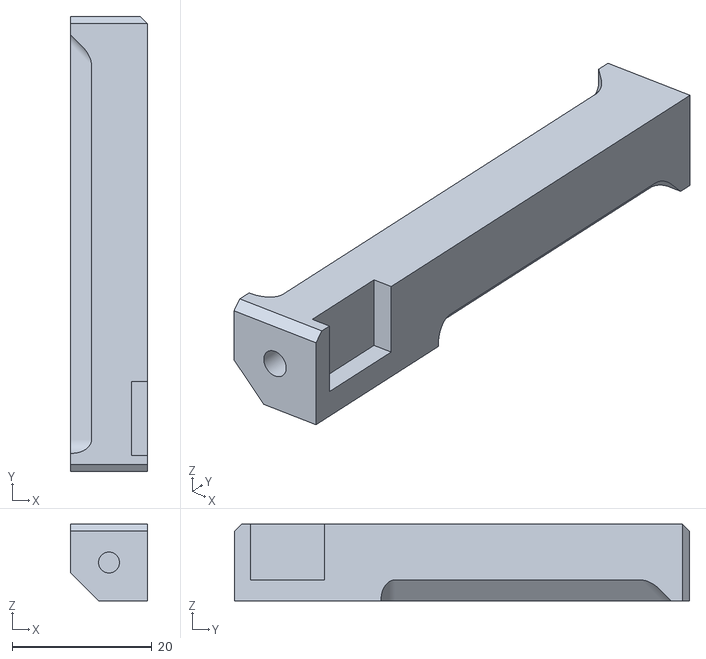
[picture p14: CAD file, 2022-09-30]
_3dprint/stl/D_pillar.stl
11.0 x 65.2 x 11.0

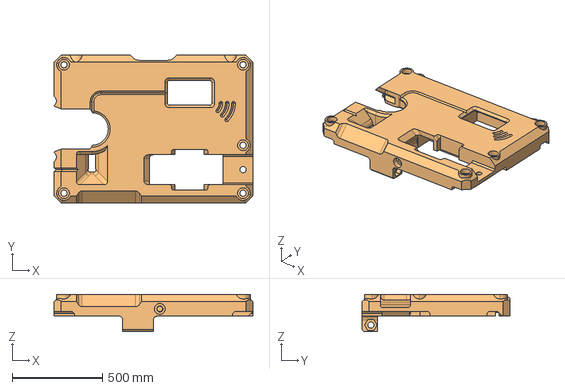
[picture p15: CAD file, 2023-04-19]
_3dprint/source/E-TKT_025-structure_J_top.stp
1100.0 x 820.0 x 205.0 mm

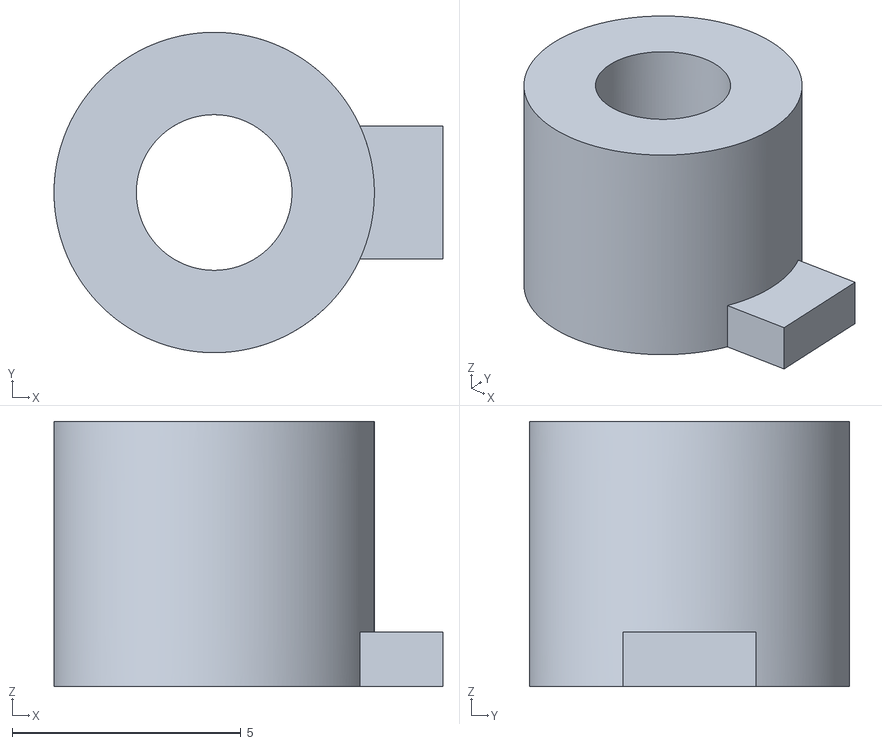
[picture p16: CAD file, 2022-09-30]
_3dprint/stl/N_wheel_coupling_bottom.stl
8.50 x 7.00 x 5.80

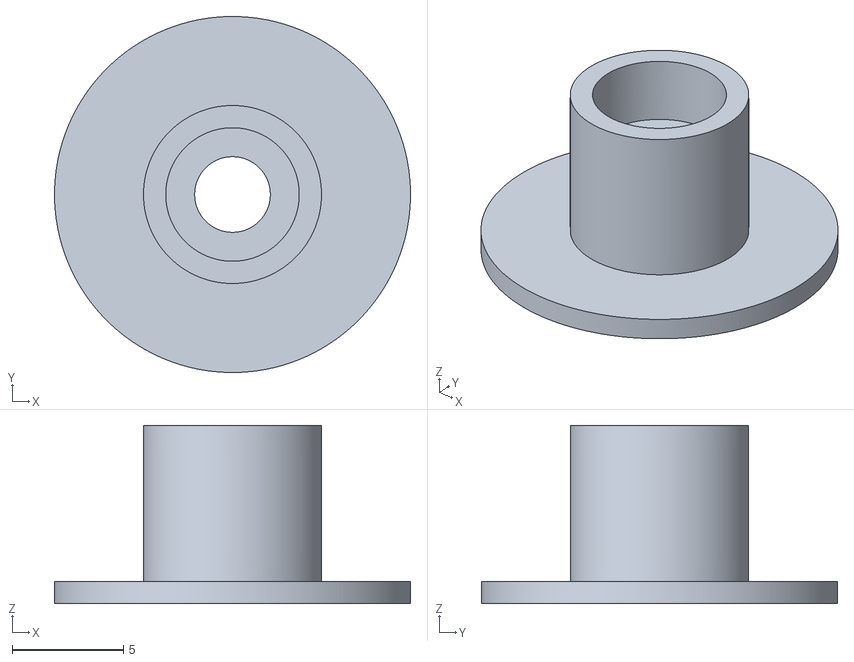
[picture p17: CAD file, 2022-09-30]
_3dprint/stl/O_wheel_coupling_top.stl
16.0 x 16.0 x 8.00

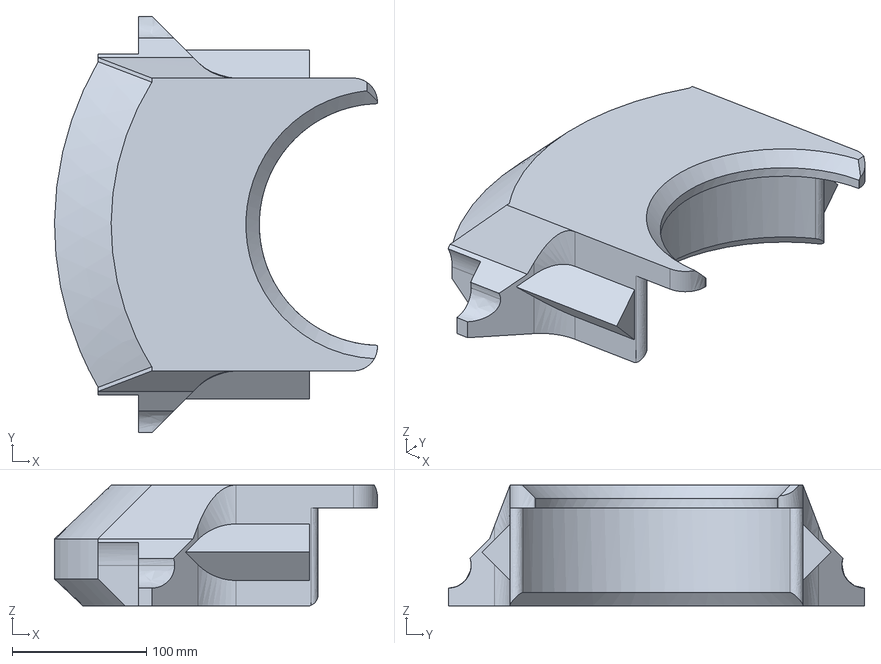
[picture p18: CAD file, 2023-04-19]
_3dprint/source/E-TKT_025-structure_M_top_wheel_cover.stp
240.5 x 310.0 x 90.0 mm

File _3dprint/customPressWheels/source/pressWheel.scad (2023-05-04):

//pressing daisy wheel for DYMO label tabe

/*maybe it come in handy to calculate the deflection of the tongues (beams)
 starting point: https://mechanicalc.com/reference/beam-deflection-tables
  
  Deflection: δ = -(Fx²/6EI)*(3L-x), δmax=FL³/3EI @x=L
  Slope: Θ = -(Fx / 2EI)*(2L-x), Θmax = (FL² / 2EI) @x=L
  
  L,x: length, position [m]
  F: Force at l [N]
  E: youngs modulus [Pa]
  I: Moment of Inertia [m^4]
  
  Isquare= w*h³/12 |square([w,h]) (deflection in around y)
  
*/

/*
  About symbols and fonts
  for portability you should use the fonts embedded with openSCAD (LiberationSans,..Mono,..Serif, see Help->Fontlist)
  you can use some Unicode Characters as well by either copying them from a website or using the codes like \u263A (Smiley hex)
  e.g. https://www.vertex42.com/ExcelTips/unicode-symbols.html
  Attention! most of them will not work
*/

/* [Parameters] */
$fn=50;
//charset
charset= "custom"; //["custom","16segment"]
cstmChars = "ABCDEFGHIJKLMNOPQRSTUVWXYZÄÖÜ-.1234567890X";
//general spacing between all parts
spcng=0.2; //spacing between parts

/* [Emboss] */
//textheight above baseline
txtSize=2.5; 
//X-Y spacing between positive and negative
embXYSpcng=0.15; 
//Z spacing between positive and negative
embZSpcng=0.15; 
//embossing height
embHght=0.5; 

/* [Top Disc] */
// render a label with the characterset
rndrTopLabel=true;
//outer Dia of top disc (negative)
topDscDia=55.9; 
//Thickness of top disc
topDscThck=3;
//Center bore diameter of top disc
topCntrDia=10.8;
//Diameter of the detends
dtntDia=2;

/* [Bottom Disc] */
//outer Dia 
botDscDia=51.3; 
//thickness
botDscThck=1.2;  
//zOffset of tongues from bottom
botZOffset=2.15; 
//Diameter of the chars baseline
bsLneDia=49.2; 
//width of the slots between tongs
sltWdth=0.6; 

//Diameter of nonslotted part
sltCntrDia=22; 
//Diameter of center cylinder
botCntrDia=13.95;
//Total height of center cylinder
botCntrHght=5.2; 
//Diameter of the center bore
cntrBore=7.1; 

/* [show] */
showTopDsc = true;
showBotDsc = true;

/* [Tune] */
//apply a sectionCut 
showSection= false;
//select char to cut, 0: anvil
wheelRot=0;
//tilt the wheels to have the tip of tongue lay flat
wheelTilt= false;
showCharInTopDsc=false;

/* [Hidden] */
charTilt=8.9;
fudge=0.1;
//guide dimensions
gdWdth=2;


// -- charsets --
//16 segement LCD inspired charset, each segment alone plus some common combinations, can be combined to capital, lowercase and numbers
segmented16=[["a1"],["a2"],["b"],["c"],["d1"],["d2"],["e"],["f"],["g1"],["g2"],["h"], ["i"],["j"], ["k"], ["l"],["m"],
             ["a1","a2"],["d1","d2"],["g1","g2"],["j","k"],["a1","a2","f","e"],["d1","d2","b","c"],["h","m"],["a1","a2","b","c","d1","d2","e","f"]];

chars = (charset=="custom") ? cstmChars : segmented16;
//a polygon to revolute into the disc shape
charCount=len(chars); 
dscPoly=[[botCntrDia/2-fudge,2.15],[sltCntrDia/2,2.15],[37.6/2,2],[38.6/2,3],[botDscDia/2,2], //bottom face
         [botDscDia/2,2+botDscThck],[38.6/2-0.5,3+botDscThck],[37.6/2-0.5,2+botDscThck],[sltCntrDia/2,2.15+botDscThck],[botCntrDia/2-fudge,2.15+botDscThck]];
tngAng=360/(charCount+1); //angle of one tongue

lngGuide=botCntrDia+3.3;
shrtGuide=botCntrDia;
sectZRot = wheelRot ? wheelRot*tngAng : 0;
sectYTilt = wheelTilt ? -charTilt : 0;

if (showTopDsc){
  rotate([0,sectYTilt,0]) difference(){
    rotate(sectZRot) topDsc();
    if (showSection) color("darkred")
      translate([0,-(topDscDia/2+fudge)/2,botCntrHght+topDscThck/2]) 
        cube([topDscDia+fudge,topDscDia/2+fudge,topDscThck+fudge],true);
    }
}
if (showBotDsc) 
  rotate([0,sectYTilt,0]) difference(){
    rotate(sectZRot) botDsc();
    if (showSection) color("darkred")
        translate([0,-(botDscDia/2+fudge)/2,(botCntrHght+topDscThck)/2]) 
          cube([botDscDia+fudge,botDscDia/2+fudge,botCntrHght+topDscThck+fudge],true);
    }
//tuning: show the chars as if they where pressed into the top disc    
if (showCharInTopDsc)
  rotate([0,sectYTilt,0]) difference(){
    color("ivory") for (i=[0:len(chars)-1])
      rotate(tngAng*i+tngAng+sectZRot) translate([bsLneDia/2,0,botCntrHght]) 
        rotate([0,0,90]) linear_extrude(embHght,convexity=3) 
          text(chars[i],size=txtSize, halign="center");
    if (showSection) color("darkred")
      translate([0,-(topDscDia/2+fudge)/2,botCntrHght+topDscThck/2]) 
        cube([topDscDia+fudge,topDscDia/2+fudge,topDscThck+fudge],true);
  }

//debug tongue cross section
*polygon(dscPoly);

module topDsc(){
  lblThck=0.2;
  //top disc with negatives
  color("darkSlateGrey") translate([0,0,botCntrHght]) 
    difference(){
      linear_extrude(topDscThck,convexity=3)
        difference(){ //2D difference
          circle(d=topDscDia,$fn=charCount+1);
          //center
          circle(d=topCntrDia);
          //detents
          for (ang=[0:tngAng:360-tngAng]) 
            rotate(ang) translate([topDscDia/2,0,0]) circle(d=dtntDia);
          //guides
          hull() for (ix=[0,1])
            translate([ix*(shrtGuide-gdWdth)/2,0])
              circle(d=gdWdth+spcng);
          hull() for (iy=[0,1])
            translate([0,iy*(lngGuide-gdWdth)/2])
              circle(d=gdWdth+spcng);
        }
      //groove for labels
      if (rndrTopLabel)
        rotate_extrude() translate([bsLneDia/2-txtSize*1.25,topDscThck-lblThck,0]) 
          square([txtSize*1.5,lblThck+fudge]);
          
      //chars 
      for (i=[0:len(chars)-1])
          rotate(tngAng*i+tngAng) translate([bsLneDia/2,0,-fudge]) 
            rotate([0,0,90]) linear_extrude(embHght+embZSpcng+fudge) 
            if(charset=="custom")
              offset(embXYSpcng) text(chars[i],size=txtSize, halign="center");
            else if (charset=="16segment")
              offset (embXYSpcng) sixteenSegment(size=2.5, draw=segmented16[i]); 
              
    }
    //labels
    color("yellow") if (rndrTopLabel){
        for (i=[0:len(chars)-1])
          rotate(tngAng*i+tngAng) translate([bsLneDia/2,0,topDscThck+5]) 
            rotate([0,0,90]) linear_extrude(lblThck) 
            if(charset=="custom")
              text(chars[i],size=txtSize, halign="center");
            else if(charset=="16segment")
              sixteenSegment(size=2.5, draw=segmented16[i]);
    }
}

module botDsc(){
  //disc with tongues and positives
  
  //center dome
  color("ivory") rotate(-tngAng/2) linear_extrude(botCntrHght) difference(){
    circle(d=botCntrDia,$fn=charCount+1);
    circle(d=cntrBore);
  }
  //guides in topDsc
  color("ivory") translate([0,0,botCntrHght]) rotate(-tngAng/2) difference(){
    union(){
      cylinder(d=topCntrDia-fudge*2,h=topDscThck,$fn=charCount+1);  
      //guide bars
      //short
      rotate(tngAng/2){
        hull() for (ix=[0,1])
          translate([ix*(botCntrDia-gdWdth)/2,0,0]){
            cylinder(d=gdWdth,h=topDscThck-gdWdth/2);
            translate([0,0,topDscThck-gdWdth/2]) sphere(d=gdWdth);
          }
        //long
        hull() for (iy=[0,1])
          translate([0,iy*(lngGuide-gdWdth)/2,0]){
            translate([0,0,-(botCntrHght-botZOffset)]) 
              cylinder(d=gdWdth,h=topDscThck-gdWdth/2+(botCntrHght-botZOffset));
            translate([0,0,topDscThck-gdWdth/2]) sphere(d=gdWdth);
          }
        }
      }
      translate([0,0,-botCntrHght-fudge/2]) cylinder(d=cntrBore,h=topDscThck+botCntrHght+fudge);
    }
  
  //rotate extrude the cross section and cut slots
  color("ivory") rotate(-tngAng/2) difference(){
    rotate_extrude($fn=50/*charCount+1*/) polygon(dscPoly);
    //slots
     for (ang=[0:tngAng:360-tngAng]){
      sltLngth=(ang<tngAng*2) ? (botDscDia-sltCntrDia)/2-3 : (botDscDia-sltCntrDia)/2;
      sltOffset = (ang<tngAng*2) ? 3 : 0;
      rotate(ang) translate([(sltCntrDia+sltLngth+fudge)/2+sltOffset,0,botCntrHght/2]) 
        cube([sltLngth+fudge,sltWdth,botCntrHght-fudge],true);
    }
  }
  //anvil
  color("ivory") translate([botDscDia/2+1.4,0,3]) 
    rotate([0,charTilt,0]) translate([-8.3,-1,-botDscThck]) 
      cube([8.3,2,botDscThck+0.7]);
      
  //chars
  color("ivory") for (i=[0:len(chars)-1])
    rotate(tngAng*i+tngAng) translate([bsLneDia/2,0,3.4-0.2]) // z-Offset to connect chars to tongue tipp securely
      rotate([charTilt,0,90]) 
        linear_extrude(embHght+0.14, convexity=3) //compensate for z-Offset of chars
        if(charset=="custom")  
          text(chars[i],size=txtSize, halign="center");
        else if(charset=="16segment")
          sixteenSegment(size=2.5, draw=segmented16[i]);
        
}
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

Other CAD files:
_3dprint/stl/I_nema_wheel_hub.stl
_3dprint/source/E-TKT_025-electronic_stepper_NEMA-17HS4023.stp
_3dprint/stl/F_pillar.stl
_3dprint/source/E-TKT_025-structure_O_wheel_coupling_top.stp
_3dprint/source/E-TKT_025-electronic_external models_28BYJ-48 - 5V by Pablo Galarce.stp
_3dprint/source/E-TKT_025-electronic_external models_MG-995 by Hasanain Shuja.stp
_3dprint/source/E-TKT_025-electronic_external models_OLED TFT 0.96 inch 64x128 by Mih Kov.stp
_3dprint/source/E-TKT_025-electronic_hall_sensor_KY-003.stp
_3dprint/source/E-TKT_025-mechanic_bearing_608-2Z.stp
_3dprint/source/E-TKT_025-mechanic_bearing_623-2Z.stp
_3dprint/source/E-TKT_025-mechanic_daisywheel_MOTEX-43chars.stp
_3dprint/source/E-TKT_025-mechanic_extruder_gear_MK8-40-teeth-5mm-axis.stp
_3dprint/source/E-TKT_025-mechanic_m3.stp
_3dprint/source/E-TKT_025-mechanic_m3_hex_nut_DIN-EN-ISO4032-M3.stp
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

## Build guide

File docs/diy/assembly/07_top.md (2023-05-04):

---
layout: default
title: 7. top
description: "E-TKT"

parent: 🧩 assembly
grand_parent: 🛠️ do it yourself!
nav_order: 8
---

# **7. top**

----

💬 *whenever you need, check out the [exploded view](https://andreisperid.github.io/E-TKT/diy/assembly/assembly.html) for orientation;*

----

## top + display

_DSC0588
_DSC0589
_DSC0591
_DSC0592

1. place the OLED display into the craddle, with the wires to the outmost part of the J_top piece;
2. cover it with the K_top_screenholder;
3. progressively tighten each of the 2x m3x6mm screws to make sure the screen is flat (check the outside).

## top + LEDs

_DSC0593
_DSC0594
_DSC0597
_DSC0598
_DSC0599
_DSC0600
_DSC0601
_DSC0603

1. pass the flat cables for both DIP LEDs through the pathway;
2. "click" the LEDs into their slots, and you might need carefully to cut a bit of material just enough to make sure it fits firmly;
3. using a flat plier might help pressing them;
4. strech the cables and make sure no segments are falling outside the boundaries, otherwise the daisy wheel might be prevented from spinning;
5. crimp the dupont connectors observing the polarity: arrows shoud be ground;
6. place 2x 2-via 2.54mm caps.

## top + LEDs & display + PCB

_DSC0604
_DSC0606
<!-- ![_DSC0608](https://user-images.githubusercontent.com/15098003/196253533-e1907be1-fbb9-40e1-ba28-b42fdab4cede.jpg) -->
_DSC0610

1. connect the LEDs connectors;
2. then the display connector;
3. carefully close the K_top_screenholder while observing the PCB, servo and B_walland their respective fittings;

## top + servo

_DSC0611
_DSC0612
_DSC0613

1. place one nut into the servo slot of the J_top;
2. place one m3x20 with a washer to fix the servo;
3. while you firmly grip the J_top against the A_bottom, press the servo inward and tighten the screw;

## top + pillars

_DSC0614
_DSC0615

1. place 4x m3x20screws to attach the J_top vertically to the pillars and wall;
2. finish by using 2x m3x16 screws on the side.

## result

_DSC0616

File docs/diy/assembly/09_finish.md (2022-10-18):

---
layout: default
title: 9. finish
description: "E-TKT"

parent: 🧩 assembly
grand_parent: 🛠️ do it yourself!
nav_order: 10
---

# **9. finish**

----

💬 *whenever you need, check out the [exploded view](https://andreisperid.github.io/E-TKT/diy/assembly/assembly.html) for orientation;*

----

These are the few last steps.

PS: the wheel cover serves for removing the daisy wheel without needing to disassemble anything else.

## wheel cover

_DSC0630
_DSC0634

1. slide the M_top_wheel_cover into the J_top;
2. use 2x m3x10 screws to lightly touch the bearing, but we will finish tightening them on the final step;

## D_pillar

_DSC0635
_DSC0636
_DSC0638

1. use 2x m3x20 screws to fix the D_pillar against the A_bottom and J_top;

## wheel hub height

_DSC0723
_DSC0724
_DSC0726

1. as you might already have noticed, the daisy wheel might be lose, but we needed to have the whole structure stable before adjusting it;
2. rotate the daisy wheel assembly until you find a chamfer on the bottom of the I_nema_wheel_hub;
3. place a scredriver to leverage the I_nema_wheel_hub against the H_nema_cover;
4. while keeping it up, tighten very whell both screws of the I_nema_wheel_hub;
5. also, tighten both screws on the M_top_wheel_cover;
6. test to see if the daisy wheel is properly fixed, without clearance.

## 🎈 congratulations, now we are ready to proceed to connecting it, adding a reel and finally calibrating!

_DSC0647

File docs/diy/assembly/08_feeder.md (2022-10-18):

---
layout: default
title: 8. feeder
description: "E-TKT"

parent: 🧩 assembly
grand_parent: 🛠️ do it yourself!
nav_order: 9
---

# **8. feeder**

----

💬 *whenever you need, check out the [exploded view](https://andreisperid.github.io/E-TKT/diy/assembly/assembly.html) for orientation;*

----

The feeder is a springed mechanism that helps the cog gain traction against the tape by gently denting the adhesive liner.

_DSC0619

## feeder + bearing

_DSC0620
_DSC0621
_DSC0622
_DSC0623
_DSC0624

1. surround 2x 623ZZ bearings with 2x washers, one on each extremity;
2. slide them into the L_top_tapefeeder;
3. use one m3x16 screw and carefully insert it, making sure to have the washers aligned on both ends;
4. place a nut on the other side and then tighten the screw.

## feeder + top

_DSC0625
_DSC0626
_DSC0627

1. put the L_top_tapefeeder into its slot in J_top;
2. use one m3x40 transversally to reach the B_wall on the other end, and tighten it;
3. pick one m4x10 screw and lightly attach against the J_top through to the upper hole of the L_top_tapefeeder;
4. do not tighten it yet, just enough to keep it in place.

## result

_DSC0628

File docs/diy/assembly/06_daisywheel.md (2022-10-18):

---
layout: default
title: 6. daisy wheel
description: "E-TKT"

parent: 🧩 assembly
grand_parent: 🛠️ do it yourself!
nav_order: 7
---

# **6. daisy wheel**

----

💬 *whenever you need, check out the [exploded view](https://andreisperid.github.io/E-TKT/diy/assembly/assembly.html) for orientation;*

----

The leading character of the device, the daisy wheel is responsible for embossing the letters into the tape.

_DSC0576
_DSC0577

1. start by picking the device from the side, as indicated above;
2. make sure the magnet on the I_nema_wheel_hub is facing the hall sensor, which also means the both I_nema_wheel_hub screws are are looking to you;
3. ***pay attention now*** 
4. align the bottom part of the daisy wheel (with the teeth) to have the letter "J" facing the P_press on the right;
5. that will also mean the wheel's only big tooth (for cutting) will be facing you, together with to both I_nema_wheel_hub screws;
6. "click" the daisy wheel into the I_nema_wheel_hub;

## wheel coupling bottom

_DSC0582
_DSC0581

1. now, place the top part of the daisy wheel, observing the alignment fittings;
2. then, place the N_wheel_coupling_bottom in the hole while respecting the alignment mark;

## wheel coupling top

_DSC0583
_DSC0584
_DSC0585
_DSC0586

1. insert the 608ZZ bearing into the O_wheel_coupling_top;
2. from the other side, insert one m3x16 screw;
3. while firmly holding the daisy wheel assembly, tighten the screw until there is no clearance.

## result

_DSC0587

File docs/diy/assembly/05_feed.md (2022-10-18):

---
layout: default
title: 5. feed
description: "E-TKT"

parent: 🧩 assembly
grand_parent: 🛠️ do it yourself!
nav_order: 6
---

# **5. feed**

----

💬 *whenever you need, check out the [exploded view](https://andreisperid.github.io/E-TKT/diy/assembly/assembly.html) for orientation;*

----

The 28BYJ is a reduced stepper motor and it's responsible for feeding the tape forward through the guiding track.

_DSC0561

## 28BYJ + gear

_DSC0562

1. place the gear into the stepper axis;
2. pay attention to the chamfer: one of the screws must face it;
3. tighten both screws;

## + wall 

_DSC0564
_DSC0565
_DSC0567

1. put the 28BYJ stepper into the B_wall;
2. place two nuts into the slots;
3. from the other side, tighten 2x m3x6 screws;
4. as with the stepper, it is recommended to wrap the excess cables for this stepper motor with wire strap.
5. connect the cable to the PCB with the red to the left, when facing the PCB;

## + chassis

_DSC0568
_DSC0569
_DSC0570

1. place the B_wall into the A_bottom;
2. the stepper cable should not pass the further away as possible from the NEMA axis;
3. organize the cables on the other side;
4. fix both parts together by using 2x m3x20 from underneath.

## + wall_track and D_pillar

_DSC0572
_DSC0573
_DSC0574

1. now, keep the C_wall_track into the B_wall while attaching the D_pillar;
2. observe the servo cable while doing it;
3. fix the D_pillar with one m3x20 screw.

## result
_DSC0575

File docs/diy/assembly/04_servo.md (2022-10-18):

---
layout: default
title: 4. press
description: "E-TKT"

parent: 🧩 assembly
grand_parent: 🛠️ do it yourself!
nav_order: 5
---

# **4. press**

----

💬 *whenever you need, check out the [exploded view](https://andreisperid.github.io/E-TKT/diy/assembly/assembly.html) for orientation;*

----

The servo, together with the hall sensor, is one of the most critical sub systems of the device.

***Please, be focused and follow thoroughly.***

_DSC0539

## servo: connection

_DSC0540

1. it is advisable to roll the excess cable with a wire strap to keep it tidy;
2. the correct connector order when facing the PCB is: GND (brown), VCC (red), SIGNAL (orange);
3. use an allen key to help push it to the header.

## servo: homing

Servos receive PWM signals to reach directly to a specific angle, in this case from 0 to 180 degrees.

It is unpredictable in which angle a given unit is delivered to you. Because of that, we'll be turning the machine on to make sure it is homed in the resting angle.

_DSC0542
_DSC0545

1. make sure you have already flashed both the firmware and data files (SPIFFS) into the PCB;
2. connect the display to the PCB;
3. plug the 12DC power source into the PCB;
4. wait for the "E-TKT" splash animation and the servo will be homed to its resting position.

## press

_DSC0547
_DSC0548

1. place a m6 washer into the P_press;
2. this is intended to ease the movement between the P_press while keeping it perpendicular to the servo axis;

## press: alignment

Now that the servo is homed, we can put the P_press by using its own visual cue.

_DSC0549
_DSC0550

1. don't forget to keep the device connected to the power source;
2. place the servo on a surface longitudinally;
3. use the lateral line of the P_press to keep it aligned;
4. aim the P_press hole to the servo hub and press gently until fitting it;
5. *do not twist, we need to "carve" the P_press plastic to the "cog" shape of the hub!*
6. place an m3x6 with washer and screw tightly
7. there must be absolutely no lateral play (force it a bit to test) between the servo and the P_press, otherwise it will miss the daisy wheel's tooth when forced. 

## chassis

_DSC0551
_DSC0556
_DSC0557
_DSC0558

1. disconnect the power source from the PCB;
2. remove the display and reserve it;
3. to ease mounting the servo on the A_bottom, place 2x nuts and pass 2x m3x20 with washers;
4. screw both lightly, just to grab the nuts onto the other side;
5. keep a gap between the washers and the A_bottom;
6. align the servo to both screws and "click" it through;
7. tighten both screws while making sure the servo is as inward and pressed against to the A_bottom as possible;

## result & check

Just to make sure the P_press is aligned: with the machine turned off, twist the press a bit and turn the device on again.

***It should home to rest position. That means the lateral of the P_press should be 100% vertical, together with the servo outline.***

If not, you will need to print another P_press and repeat the previous steps.

_DSC0559
_DSC0560

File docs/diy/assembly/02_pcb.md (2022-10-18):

---
layout: default
title: 3. PCB
description: "E-TKT"

parent: 🧩 assembly
grand_parent: 🛠️ do it yourself!
nav_order: 3
---

# **2. PCB**

----

💬 *whenever you need, check out the [exploded view](https://andreisperid.github.io/E-TKT/diy/assembly/assembly.html) for orientation;*

----

The PCB gathers electronic breakouts but also serves a structural role. That means it is adjacent to several mechanical parts.

_DSC0521

## PCB + stepper driver

_DSC0523

1. place the A4988 driver on the board, observing the VMOT and GND markings to make sure it is properly oriented;

## PCB + hall sensor

_DSC0524

1. place the hall sensor;
2. it isn't going to hold steadily into the connector and that's expected;

## + F_pillar

The F_pillar will make sure the hall breakout stays firm in position, while at the same time aggregating the PCB to the overall structure.

_DSC0526
_DSC0527
_DSC0528

1. place two nuts in the F_pillar slots;
2. slide the F_pillar from the PCB side;
3. insert 2x m3x10 with 2x washers and fasten them;

## + NEMA + G_pillar

_DSC0529
_DSC0530

1. connect the NEMA harness to the stepper motor;
2. then, connect it to the PCB;
3. mount the G_pillar in the opposite side of the PCB;
4. very carefully, place the assembly into a surface. 

## result

_DSC0531

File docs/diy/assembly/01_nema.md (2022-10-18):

---
layout: default
title: 1. NEMA
description: "E-TKT"

parent: 🧩 assembly
grand_parent: 🛠️ do it yourself!
nav_order: 2
---

# **1. NEMA**

----

💬 *whenever you need, check out the [exploded view](https://andreisperid.github.io/E-TKT/diy/assembly/assembly.html) for orientation;*

----

_DSC0500

In this first step, we will prepare the NEMA stepper sub-module, responsible for the daisy wheel character selection.

## cover

_DSC0502
1. place the H_nema_cover on top of the NEMA stepper motor, and fix it with 4x m3x6 screws.

## magnet polarity

We need to know the right magnet polarity to trigger the hall sensor, otherwise the device will not be able to home itself.

_DSC0505
_DSC0506

1. for that, temporarily mount the hall sensor breakout into the PCB and turn it on;
2. avoiding any short circuits, pass the magnet extremities to the sensor, **careful, as it might be attracted to the terminals**;
3. when the right side is found, mark it with a pen;
4. turn the PCB off and then disassemble the hall sensor breakout;

## wheel hub: magnet

_DSC0508
_DSC0509

1. with the help of a plier, place the magnet into the I_nema_wheel_hub with the mark outside;
2. the magnet must be leveled to the surface, otherwise it might hit the sensor when rotating;

## wheel hub: fixation

_DSC0515
_DSC0516
_DSC0518

1. now, place 2x m3 nuts into the slit underneath the I_nema_wheel_hub;
2. a plier is helpfull for the initial insertion, then an allen wrench helps to slide it in;
3. be careful with the second nut, otherwise it may go beyond its proper spot;
4. place 2x m3x8 screws just to make sure they grab the nuts, but do not fasten them yet;

## NEMA + wheel hub assemble

_DSC0519

1. slide the cube to the stepper motor, making sure the chamfer matches both parts;
2. if you have having trouble, make sure the screws are not tightned;
3. again, do not fasten the screws, we will have then tightened later.

## result

_DSC0520

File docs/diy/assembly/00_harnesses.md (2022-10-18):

---
layout: default
title: 0. harnesses
description: "E-TKT"

parent: 🧩 assembly
grand_parent: 🛠️ do it yourself!
nav_order: 1
---

# **0. harnesses**

----

💬 *whenever you need, check out the [exploded view](https://andreisperid.github.io/E-TKT/diy/assembly/assembly.html) for orientation;*

----

_DSC0484

In this first step, we will prepare several parts that will be used through all the assembly, interacting with multiple subgroups.

## hall sensor breakout

_DSC0490

1. if the breakout has a male header, remove it first with care;
2. solder a 3x pin female 2.54mm header to the breakout's back face;
3. fold hall terminals by 90° at approximately 7mm from the board, making sure the sensor is perpendicular to the breakout;

## OLED display + harness

_DSC0486

1. if the breakout has a male/female header, remove it first with care;
2. solder a 4x vias flat cable directly to the breakout (there is no space for a header when assembled);
3. ***OBSERVE THE WIRING: in this specific display model, the VCC and GND needs to be switched***;
4. crimp 4x female 2.54mm connectors;
6. as in the above photo point of view, the vias must be: SDA, SCL, VCC, GND.
5. place a 4x plastic case *(nevermind the 5x connector case, I didn't have 4x available)*;

## NEMA harness

_DSC0488

1. cut the original 4 vias stepper cable to use the extremity that connects to the motor;
2. crimp 4x female 2.54mm connectors;
3. ***OBSERVE THE WIRING: the inner wires should be switched***; ;
4. place a 4x plastic case *(nevermind the 5x connector case, I didn't have 4x available)*;

## LEDs + harnesses

_DSC0491
1. cut the terminals of the two DIP LEDs;
2. solder each LED to a 2 vias flat cable
3. I recommend to use individual thermo retractable sleeves for each terminal to avoid short circuits
4. ***do not crimp the connectors yet, we will need to pass the cables before that.***

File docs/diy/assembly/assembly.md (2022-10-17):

---
layout: default
title: 🧩 assembly
nav_order: 6
description: "E-TKT"

parent: 🛠️ do it yourself!
has_children: true
---

# 🧩 **assembly**

exploded_001-01

<p align="right">
  <a href="https://user-images.githubusercontent.com/15098003/196292732-2089eaad-7a61-4db6-8097-c3a6049bdc21.png" target="_blank">
    <i>🔎 see larger</i>
  </a>
</p>

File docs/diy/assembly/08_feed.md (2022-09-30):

---
layout: default
title: 8. feed press
description: "E-TKT"

parent: 🧩 assembly
grand_parent: 🛠️ do it yourself!
nav_order: 8
---

# **8. feed press**

29. place the Y_bearings surrounded by M3 washers and fix them through with one M3x?? screw and nut;
30. position the assembled part into the X_top and use the M3x?? screw transversally until the end;
31. insert the tape into the track until reaching after the feeding cog;
32. lightly screw the M4x?? into the top hole until the tape is secured;

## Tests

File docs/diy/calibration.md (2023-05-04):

---
layout: default
title: ⏱️ calibration
nav_order: 9
description: "E-TKT"
parent: 🛠️ do it yourself!
---

# ⏱️ **calibration**

----

This final part of the process will make sure the letter alignment is finely adjusted, and together with the correct imprinting pressure.

Only when fully assembled and revised, follow the instructions to [connect the machine](https://andreisperid.github.io/E-TKT/diy/connection.html) and add a [new reel](https://andreisperid.github.io/E-TKT/diy/reel.html);

----

## **<< attention is needed here, please >>**

- reboot your E-TKT;
- after the splash screen the machine will home by rotating until the magnet meets the hall sensor;
- check the letter "J" position in the top window: if the letter is visually centered (right image), then proceed to the step 4.



***<details><summary> ⚠️ click here in case the letter "J" does not meet the above criteria, otherwise move on </summary>***  
  
_DSC0676_arrow

- **<< TURN OFF the device >>** otherwise you might short circuit the hall sensor terminals;
- delicately adjust the hall sensor position following the tangent (cyan) axis in the image:
  - if "J" is too much to the right, push the hall sensor inward the device (yellow);
  - if "J" is too much to the left, pull the hall sensor outward the device (magenta);
- make sure to keep the same distance on the transversal (red) axis;
- only when the letter "J" is visually centered in the top window, you might proceed to the next step;

Also, when turning the machine on, the press angle should be at 2mm from the I_nema_wheel_hub. If not, then you might need to go back to the [press assembly procedure](https://andreisperid.github.io/E-TKT/diy/assembly/04_servo.html).
   
</details> 

----

## fine tuning

In the app, click on "SETUP".

You will see a xray of the machine, and now we will proceed to the first part of the calibration: the alignment (magenta).

app_setup

### Alignment

_DSC0678
*The image above shows the exact moment the press is moved to the tooth.*

- the align values ranges from 1 to 9, having 5 as a default (middle).
- now click the "TEST" button to the right side of "align";
- the machine will slowly and lightly press the daisy wheel letter;
- the goal is to have the press to be fully aligned with the character, that should also be right in the middle of the character window;
- adjust the values and test to make sure it is alright;

### Force

_DSC0730
*The image above shows several tests with progressive "force" values, and it is noticeable that up from a certain point there is no real difference.*

- now we will adjust the peak servo angle, that will determine if the letter will be lightly or heavily pressed against the tape;
- the default value is 1 in a scale from 1 to 9;
- increase it one at a time and hit the big test button;
- take the opportunity to see if the alignment is correct, and if not adjust it too;

---

### 🕐 when you are happy with the result, click save and wait for the machine to reboot.
<br>

# 🎉 **you are now ready to label around!** 🎉

<br>

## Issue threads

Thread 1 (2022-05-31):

Wrong character printed

andreisperid, 2022-05-31:
The machine seldom mistakes the correct letter (rare), seems related to processing hiccups.

Closed 2023-02-25.

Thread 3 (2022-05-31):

Wrong status on web app

andreisperid, 2022-05-31:
Sometimes the status feedback (reel, cut, feed, print) does not update correctly and gets stuck.

Closed 2022-10-05.

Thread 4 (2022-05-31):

Loading delay/problem with the web app

andreisperid, 2022-05-31:
Frequently the font serving from the ESP32 takes more time than usual and the web app starts without the correct aspect, eventually getting stuck in that state.

Closed 2022-10-05.

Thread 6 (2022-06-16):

Excessive flexing of the structure while pressing

andreisperid, 2022-06-16:
As in https://hackaday.com/2022/06/15/diy-automated-printer-kerchunks-out-classic-embossed-labels/#comment-6484189

Suggestions: https://www.youtube.com/watch?v=F0E5adLQ-AY&lc=UgwwJ4s63TFKkHuZJst4AaABAg

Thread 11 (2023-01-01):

Error loading label font in the web-ui

sabeechen, 2023-01-01:
The printer website gets a 404 when attempting to load the label font, ```fontwhite.tff```.  This is because the file uploaded in SPIFFS is named ```fontWhite.tff``` with a capital ```W```.

Closed 2023-01-07.

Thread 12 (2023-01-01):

Printer website requires reloading if it gets suspended while printing

sabeechen, 2023-01-01:
If the printer website is suspended while its printing, it remains in the "busy" state after coming back online even if the print is finished and allows no further interaction.  Reloading the page resolves the issue.  This is particularly a problem on mobile devices, because the page is typically suspended when the screen goes to sleep.

Closed 2023-02-08.

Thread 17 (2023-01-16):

Allow printing longer labels

sabeechen, 2023-01-16:
I often find myself wanting to print labels longer than the maximum 18 or 20 characters enforced by the printer website, so I'm making this issue a starting point to discuss how to implement that.  To me it looks like there are two main things that would need to be changed to accomodate this:
1. The "PRINTING" screen on the microcontroller would need to be changed to indicate the progress of a label that doesn't entirely fit on the little oled screen.
2. The label-dependent-jingle should shorten itself somehow for very long labels.  Otherwise it just kind of drones on for an uncomfortably long time and doesn't feel "fun".
3. The website would need to be changed to also render its textbox in a way that doesn't choke for longer strings.  This should be done in a way that doesn't impede its currently very mobile-friendly sizing.

sabeechen, 2023-01-16:
To handle (1), here is what I've come up with for changes to the PRINTING screen:

- Add a thin border to the label text, to clearly indicate where the start and stop of the label is.
- As the label prints, scroll the label left when necessary to keep the current point of printing progress in frame.
- When the label text bleeds off either side of the screen, render a "jagged edge" as a visual indication that the label doesn't end there.
- Increase the character spacing by 1px for readability and to better replicate the final print spacing.

Here is a demo I've made that shows this in practice for a long label:
https://photos.app.goo.gl/2bAFpN6qahmURqno8

And here is a demo showing how it looks with a shorter label.
Bonus enhancement: I also made it render glyphs for the special characters (♡☆♪€) instead of the ASCII replacement characters.
https://photos.app.goo.gl/mQt8DijTwiNLRGek8

In addition to allowing longer labels to be printed, I think this makes the screen feel like its "simulating" the physical label being printed a bit better.  @andreisperid, what do you think?

andreisperid, 2023-02-07:
Hi Stephen 👋

That's an interesting demand and I understand that sometimes we just need longer labels :)

----

### 1 — device

Your solution works very well. Maybe for the visual indication we could use "..." instead of the jagged edge, because the latter might lead the user to think that's a cutting point.

Maybe something (schematically) like this:
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
PS: notice the "..." are aligned vertically to the middle and outside the borders, to make sure they are not part of the label's content.

We'd loose some space, but it makes for clarity... What do you think?

The overall readability is much better!

... and about the glyphs, AMAZING 🎉 ! That clunky characters really bothered me! How did you deal with the data transfer through network? Did you keep the characters transfer and just re-converted them for the display?

----

### 2 — music

Perhaps we could clamp the music to the first N characters. Do you think the way it is right now it too long already?

----

### 3 — web app

This is what concerns me the most, as we'd need a way to easily pan sideways... I tend to think a tridimensional or skeuomorphic approach might work, this way we could compress the extremities. Check out this ref (ingenious!) https://youtu.be/mNow_mqMSRI?t=197 (more here if you want 🤓 https://jackrusher.com/classic-ux/)

sabeechen, 2023-02-17:
I'll give a shot at putting ellipses on the oled screen and see how it looks.  Maybe they only need to be on the right, to save space?  I don't think that would introduce ambiguity about whats going on.  I made the glyphs work by making the webserver multicharacter unicode-aware, which was simpler than it sounds.  The hard part was getting everything to display correctly using different glyphs from different fonts with different heights and widths.   I'll probably put this into a separate PR and check it in, since its useful separately.

For the music, I think maybe 15 notes should be the max?  that makes the jingle a couple seconds.  I think the song should always be the same for the same label and always different for different labels, so I'm thinking something that compresses multiple characters into a single note (with some kind of deterministic hashing)  for longer labels makes sense.  I'll try out a few algorithms and try to keep it simple.

In the web app, I don't think you can do much to visually distorts the label textbox without writing a completely custom control.  Browsers seem to be pretty limited in how you can style a textbox, though I don't have a lot of in-depth knowledge about it, input elements are deceptively complex.

sabeechen, 2023-02-17:
How about like this (with some dramatic shaky cam!):
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

sabeechen, 2023-02-17:
Although I like the jagged edges a little bit more, I don't feel very strongly about it and think both are clear and work well.  I kind of like only having one side show a continuation indicator ("..." or a jagged edge) since it conveys there is work to be done to the right and none to the left.

andreisperid, 2023-02-25:
Amazing @sabeechen

The visual solution is neat!

Regarding the music: what about 16 notes total instead of 15? My amateur musician background is screaming to have four 4/4 measures :P

The idea to create a compressed music is nice. Perhaps we could create a seed from the hash to distribute the time measures inside these four 4/4 measures. Pretty modular...

About the longer label, maybe a horizontal scrollbar will do it, what do you think? Or any other kind of cue that shows that there is more content than visible, at the same time allowing for easily knowing what you are seeing and navigating laterally.

sabeechen, 2023-02-27:
For the screen: sounds good to me.  I'll make a PR that combines the symbol support and "..." scrolling (its pretty tedious to separate them).

16 notes sounds fine to me.  I'm afraid I don't understand what you mean by distributing the time measures.  Do you mean make some notes longer, producing a more varied melody?  Or perhaps that the jingles would always be in multiples of 4 notes?

A scrollbar would probably be easiest :)  Although each browser engine handles scrollbar customization in a frustratingly different way, I'll play around with some CSS to see if I can make it consistent across platforms without using one of those [bulky libraries](https://bashooka.com/coding/javascript-scrollbar-plugins/).  I'll handle this last I think, CSS is the devil.

andreisperid, 2023-02-27:
No problem for combining both issues together.

For the time measures, perhaps for now we can just clip the tones beyond 16 characters, what do you think?

Regarding the scrollbar, all right! If you want, in this case we might collaborate in a separate branch to experiment a few solutions together. For instance: where should be the bar (above or below), the visual aspect, the size, etc... Then after we find out a nice combination, we can merge back in the master branch.

sabeechen, 2023-03-30:
This sounds good to me.  I'll make a branch we can both edit at will, when we land on a solution we can just squash merge the changes into main.

I've done a little experimenting with whats possible.  It seems like there are a couple different paths we could take:

- Use the native scrollbar: This is the simplest solution, but the limiting factor will be Firefox, which only allows very limited customization of the scrollbar.  It lets you choose between two widths (thick and thin), choose the track and thumb colors, and is always anchored to the bottom for horizontal scrolling.  To have a consistent appearance across browsers, we would need to style chrome/safari to match firefox's style.
- Use a custom scrollbar library (eg [simplebar](https://grsmto.github.io/simplebar/)).  I haven't tried it out, but seem to be how most websites do it to get browser consistent scrollbars.  Its just a 5kb javascript file, so maybe that would end up being easier?
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
andreisperid, 2023-04-24:
Wow, impressive @sabeechen ! It is really neat and your attention to details is amazing!

Just thinking here about how we could keep everything below the text box in the same place independently if there is a scrollbar or not. Right now everything is pushed below.

Maybe compute the height for the "text-form-scroll", then recalculate it's own margin?

sabeechen, 2023-04-25:
Done [here](https://github.com/sabeechen/E-TKT/commit/91e898e78c4cde490400c29345b95188fbc7e61c), though I accomplished it by setting the margin of ```#text-form-border``` instead.  I also got rid of the height shifting when printing starts/finishes.

andreisperid, 2023-04-25:
That's great Stephen, thank you!

I was reviewing our whole discussion and the music was left to be done - a65b424

And I felt maybe it would be a good idea to limit the number of chars input to 247 per round, which falls just below 1 meter (helps keep the length preview under under 999, avoid the extra digit that breaks the layout) - ad83a29

Do you want to create a pull request for me to merge? Or is there anything else you would like to do before closing the issue?

andreisperid, 2023-04-25:
While testing here I thought that it would be a nice idea to add a click functionality to the "..." so they jump to the extremities. It might be useful with super lengthy labels.

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

sabeechen, 2023-04-28:
Its a nice convenience feature, I think.  Mind if I add a slight highlight to the "..." background shadow on hover?

I completely forgot about the music!  I see you already submitted the change to limit to 16 characters, but I want something more fun!  Some options I've been considering:

- *Idea 1*: Any label under 10 characters is unchanged.
  For longer labels the length of each note gradually shortens from 50ms/note to 5 ms/note starting at the 5th character/note.  The idea would be to make a very longer label (30-50 ish character) play for less than a second and cescendo into a caucaphony.  I'd need to experiment to see if it actually sounds good naturally.
- *Idea 2*: "Compress" anything longer than 16 notes into 16 notes.  Id iterate through the label, alternating forwards and backwards, and re-hash each character into a different note.  so for a 17 char label (vs 16), only the last note would be different, for 18 characters, the last two would be different and so on.  This would have the advantage of sounding very similar to the way notes play now.

sabeechen, 2023-04-28:
Oh and naturally:
- Option 3: Leave as is, 16 note cutoff works fine.

sabeechen, 2023-04-28:
I've got some samples of speeding up the music (audio only).  I played around with different speeds and feel like this matched what I had in my head initially:
- Longest note is 100 ms
- Shortest note is 20ms
- After the 16th note, each note is 2ms shorter
- Pause is always 1/2 the note duration

### Label: "Short Label"

https://user-images.githubusercontent.com/21026774/235263355-4913644f-f6ee-4dd5-9d13-25be963bc6be.mp4

### Label: "longcat can be really long but only if you scratch his belly" (62 chars)

https://user-images.githubusercontent.com/21026774/235263441-4fb7499a-0f90-4d80-bf80-fa18cd6ca3dc.mp4

I think its kind of fun but I'm not married to it.  Hearing the crescendo and then the ker-chunk of the machine kind of fits together well, imho.  What do you think?

andreisperid, 2023-04-28:
Nice idea about the background shadow, go for it!

About the music: I love it!

And even before reading your point on the continuity between sound and the stepper, I had the same impression. That's a nice conceptual connection!

sabeechen, 2023-04-28:
Both are done.  I also configured the scroll tips to hide while printing, since the UI manages scrolling while printing.

You feel like there is anything left?  I'm eager to merge.

andreisperid, 2023-04-28:
Let's do it!

andreisperid, 2023-04-28:
Nice job @sabeechen ! 😃

Closed 2023-04-28.

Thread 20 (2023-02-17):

On iOS mobile safari the UI is unusable

sabeechen, 2023-02-17:
On mobile safari on iOS, and no other browser, the 'user-select: none' CSS attribute is interpreted as disabling an element completely.  This makes the UI unusable for the device, as text can not be entered into the label textbox and emoji buttons can't be clicked.

I'll make a PR that fixes this.

andreisperid, 2023-03-20:
@sabeechen I've just fixed a small CSS issue where the button labels became selectable (0869f2f).

I've tested on safari (macOS) and it seemed ok, but didn't on iPhone as I don't have one. Can you please check if its alright?

sabeechen, 2023-03-30:
Yup looks like its still fixed, sorry it took a while to get back to you.

As an aside, I've started using browserstack to test websites on different platforms and found it very helpful for problems like this.  They let you [use it for free](https://www.browserstack.com/open-source) if you maintain an open source repo, I think your repo would qualify.

andreisperid, 2023-03-30:
Very cool tip, thank you!

Closed 2023-03-30.

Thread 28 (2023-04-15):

New feature: support for more press wheels

skrutt, 2023-04-15:
The latest printables support changing wheels and there are also user such as myself who will want support for their own language, that has other or more characters than A-Z.

One suggestion from Andrei:
- On the settings there could be a text form to write all the 43 characters present on the wheel, so they would be supported (today there is a Regex to validate the chars) and transmitted to the machine.

in theory it should be possible to move the whole mapping into a string modified from the settings, but with the caveat that the "special" characters such as CUT, 0, 1 would need to be present and in the same place on all wheels used.

But having a regex in the settings could at least ease the experience of a somewhat arduino-savvy user, modify the character map and the string in the ui and you are done. or if there is a list of different wheels already implemented in the future, those with a "new" layout could add theirs to the list.

Also a thought, should the character map be moved into an own file? or reside in opt_config? It's a bit hidden right now.

sedorr, 2023-04-18:
Moving it into its own file and creating a bit of extra documentation for using different dasy wheels would definitley be cool. For me p. ex. it's quite hard to get a uppercase english wheel without importing it (I refuse to pay 7€ import tax for a 2,50€ item) so it would be quite handy to be able to use a european version (or the lower case version, as that is for some reason available as well...).

andreisperid, 2023-04-18:
So, these are the types of daisy wheels that I have here with me. Are we talking about the same models?
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

From left to right:
- Spec A (currently supported): alphanumeric upper-case plus ♡☆♪€@
- Spec B (@skrutt?): alphanumeric upper-case plus  ÄÖÜÅÆ
- Spec C (@sedorr?): alpha lower-case plus '"#$@♂☏♀ (and another one I'm not sure what it is right now.)

A study need to be made on compatibility with daisy wheels with differing character quantities. The Spec C has 36, instead of the original 43 with A and B.

----

For a hard coded way to make it work with any 43-char daisywheel (Spec A/B):

Firmware:
- modify the respective [characters](https://github.com/andreisperid/E-TKT/blob/main/src/LabelMaker.cpp#L137)

Web App:
- modify "regex" in the [useRegex function](https://github.com/andreisperid/E-TKT/blob/main/data/script.js#L271)

----

Now... Sketching below an idea for how it would work in an user friendly way (user configures everything through the web app).

Settings page (Web app):
- have a text input form to write all the characters present on the wheel (need to check if all special characters will be transmittable);
- by setting it, inform the validation Regex on the app (might need a local config cache file, need to see if that will work with a web app);
- transmit the character string to the machine.

Firmware:
- if a new character set is received, parse to determine the amount of characters (for instance, the lowercase daisywheel has 36 chars, instead of 43)
- save the character string to flash memory (if nothing is read from this address, assume standard characters (spec A)
- reboot, check flash memory for charset
- merge the charset to the numbers and positions (need to investigate if that can be made on the fly)
- on start, the web app must receive the charset in which the device is configured through the API.

Device:
- investigate the compatibility with number of chars different than 43.

Documentation:
- information of all available daisywheels, and how to change them (both on web app & physically on device)
- charset strings ready to be pasted on app settings, for all daisywheel Specs.

PS: for the 0/O and 1/I optimization, I guess the treatment could be kept whatever would be the daisywheel.

sedorr, 2023-04-18:
B & C is what I can get. The Motex I recently ordered Is Spec B as well.

I just searched around a bit and it seems like these three wheels are all that you can get, so you can probably get away with just making three presets to choose from.
If there are really only three variants then the only use case for allowing people to define their own charset would be for people ho actually make their own 3d printed daisy wheels.

skrutt, 2023-04-19:
Yes, i have the spec B, Nordic wheel.

I would place a vote for predefined presets(1,2,3), for "the most common"
wheels. If there are only these three, then that should be quite easy...

If needed/wanted, then have a user defined (preset 4?), Custom variant.
This can then be a future update, since it's more work and more exotic.

Just to state the obvious; you need some kind of preset or selection
between different wheels in order for changing wheels to be useful,
otherwise each time you change the wheel you also need to update the
character string and then you'd need a reference source for this.

On Tue, Apr 18, 2023, 22:41 Andrei Speridião ***@***.***>
wrote:

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

andreisperid, 2023-04-19:
You both have good points on having presets! For now I think that it might be the best approach.

... but, I was trying to thinking why I came to that over engineered solution and remembered that [David Knochenhauer](https://github.com/Knochi) suggested several months ago that we could try to create custom daisy wheels. He even programmed a parametric daisywheel on OpenScad. I will ask if he would join the discussion here.

Since I have a resin 3D printer now, I might give a shot. Not sure if a standard resin might stand the pressure needed for embossing. But imagine creating vintage embossing, with contemporary typefaces? Or whatever symbols... Cool!

So, in that way we might need a real customizable charset...

skrutt, 2023-04-19:
That would be cool! I don't have any resin printer though :(

I think the custom wheels are fully possible, and also a (or, will be) a
logical next step after implementing presets.

As a technical question, anyone know how to integrate feedback from
firmware to the webpage? As i understand it the page is fully defined from
the sipps image, and the characters used and regex will need to be handed
over from code to web. There are ofc infinite ways but what's the clean way?
- written to a sipps file by firmware?
- another endpoint for js to fetch?
- other ideas?

On Wed, Apr 19, 2023, 21:21 Andrei Speridião ***@***.***>
wrote:

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

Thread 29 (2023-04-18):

J_top overlapping features

sedorr, 2023-04-18:
On the J_top-Part there is a screw hole hitting a countersink.
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

andreisperid, 2023-04-18:
Yes, I have noticed that!

It is not ideal, but the display holder has a little chamfer to avoid interference:

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

I decided to keep it that way to avoid major redesign, while keeping the structural capability for the display holder. I could fill in the gap, but it would be so thin it wouldn't make a relevant difference.

andreisperid, 2023-04-19:
Fixed on 4d45f6b, updated STLs, STEPs, BOM and assembly instructions.

Thanks!

Closed 2023-04-19.

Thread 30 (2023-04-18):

Suggestion: Group and Lable your assemblies

sedorr, 2023-04-18:
It would be cool if you could Group and Lable your assemblies to make navigating the STEP file easier, as currently it's kind of hard to find anything since stuff like the Electronic and mechanic assembiles aren't seperated and all parts are simply named brep.

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

andreisperid, 2023-04-18:
Can you please help with that @sedorr ? It would be of great value!

sedorr, 2023-04-18:
I can try, but it would probably be much more helpful to do that in the native file + I don't really know what all the components and surfaces are.

andreisperid, 2023-04-18:
I have exported that STEP from Rhino, which works mostly with polysurfaces, groups and layers.

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

When I import it, it goes without problem and assembles polysurfaces, groups and layers. Do you have any clue if there are any import settings that might try to emulate that on Inventor? Maybe a preset for Rhino?

sedorr, 2023-04-18:
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

I tried it in Creo as well and it doesn't work.  I have a feeling that Rhino is diong the weird things since there are some parts (That I assume you imported) that are named.

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

Maybe try exporting your step files with a [different standard set](https://docs.mcneel.com/rhino/5/help/en-us/fileio/step_stp_import_export.htm), like AP214AutomotiveDesign.

andreisperid, 2023-04-18:
That's exactly the standard that I have used. My bet is that the Rhino's taxonomy does not translate to other software.

What about other formats, such as IGES? Any idea of a standard that might work for you?

sedorr, 2023-04-18:
Maybe just export all your printable parts as their own files? that would also be useful for some slicers, like PrusaSlicer, that take step directly.

andreisperid, 2023-04-19:
Hi @sedorr, I've just uploaded separated STEP files in 2c0aaad

Closed 2023-04-19.

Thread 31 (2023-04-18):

Suggestion: Post repair information on iFixit

sedorr, 2023-04-18:
Maybe consider posting stuff (Like a Teardown) on iFixit. I already created a wiki and a guide as an example for you: [Link](https://www.ifixit.com/Device/E-Tkt_Label_Printer).

andreisperid, 2023-04-18:
Cool idea, and thanks for putting the page on! I hope E-TKT has a good level of reparability 😄

Maybe the assembly instructions on reverse could characterize as a teardown. Overall, I'm just a bit afraid of spreading the information all around, it makes it hard to update. Hackaday was a strech by itself, but now I'm trying to center everything here at GitHub.

Anyways, I will add a page there for the assembly instructions, that directs to the [E-TKT documentation](https://andreisperid.github.io/E-TKT/) 😉

sedorr, 2023-04-18:
Btw. you can create a page on printables without actually uploading the 3d files. you can just post pictures and a placeholder file and then refer to your github, like [Orbion](https://www.printables.com/de/model/132522-orbion-3d-space-mouse-diy/comments) does. This will give you a bit more reach and a nice place to collect makes that you don't have to update for every minor change.

andreisperid, 2023-04-19:
That's a great idea, I'm definitely looking forward to see more makes out there ;)

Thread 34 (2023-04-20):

KiCad local library

andreisperid, 2023-04-20:
I've used symbols, components and footprints installed on my local global library.

To facilitate collaboration and further iterations, I will try to bring this library locally to the project's KiCad directory.

Knochi, 2023-04-21:
Since version 6, symbols are embedded into the KiCAD project, so you don‘t need to.
It loaded perfectly fine on my site.

https://www.kicad.org/blog/2021/12/KiCad-6.0.0-Release/

> KiCad 6.0 also features a brand-new  schematic and symbol library file format, based on the format used for KiCad board and footprint files. This new format enables long-desired features such as embedding symbols used in a schematic directly in the schematic file, so that cache libraries are no longer needed

andreisperid, 2023-04-21:
Nice, but what about the components, footprints and 3d models?

Knochi, 2023-04-21:
For footprints it’s the same.
For 3D models you can use the plugin „Archive 3D Models“

andreisperid, 2023-04-28:
So I think its alright, thanks @Knochi !

Closed 2023-04-28.

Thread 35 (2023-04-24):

Custom daisy wheels

andreisperid, 2023-04-24:
I have experimented printing @Knochi parametric design for the custom daisy wheels.

Keep in mind I'm just beginning at 3d printing with resin, there are among my first dozens of pieces. If anyone has experience with it, might be super useful.

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

Good news:
- the resin wheel characters are able to emboss the label (manually for now, using a plier since the model is not mountable into the device right now)
- it is pretty fast to print both bottom and top parts together (below 2h)

Bad news:
- I have used Anycubic's both Water-Washable Plus and Eco resins, and both are super brittle during the removal of supports. So a few teeth have gone already during the process.
- lets hope the actual embossing with the device is less harsh than the support removal, but I think it will be worse, meaning that probably the wheel will not stand the use with current settings.

----

What I have experimented with:
- **materials:** Eco resin is too oily, I didn't like both the result and process. The Water-Washable: much better, still as brittle as the first;
- **models angle to the printing base:** the bottom part works well horizontally, but the upper gets detached from the supports. I've managed to tilt it +- 20 degrees to lessen the adhesion area to the FEP. The bad news is that there was a subtle distortion on the final piece;
- **supports:** I have tried diminishing the intersection of supports to the models, but it ended up detaching them both. In the end, I have kept the default light settings for the Anycubic slicer, but increased the number of supports to avoid object distortion.

I have changed a few things on the model too:
- overall clearance between upper and bottom part
- increased the text inset height and lateral expansion on the upper wheel
- to be done: modify the bottom part with a coupling the daisywheel to the wheel cube so it can be tested with the real device (might need a custom wheel cube).

----

So, I think there might be at least two ways to tackle these issues:
1 - better suited material: I've seen [people recommend](https://youtu.be/gb_I-9UZem0?t=1590) mixing Siraya Tech's Blu and Tenacious to achieve a semi-flexible result.
2 - different design: to try not forcing a design that was meant for thermoplastics into resin. Maybe thickening the arms, for instance.

andreisperid, 2023-05-04:
Recently I disassembled my parents' old Olivetti type writer that uses a daisy wheel. @Knochi

It has a small V notch to help with the characters alignment, which happens automatically when the force is applied:

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

The MOTEX wheel does not have it, but with custom wheels it might be possible. Then, the P_press can have the counterpart.

Another interesting feature is this flexible film that holds all the teeth together:

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

Might help with the overall strength ;)

Knochi, 2023-05-04:
I will see if I can apply the V-alignment feature. For the flexible film, if it’s just a sheet metal on top of the arms, that would be difficult. But in the scad file there is a parameter to define the size of the inner, solid part. That basically defines the length of the arms.
One could do a FEM simulation of the ATMs but in the end it’s try and error anyway.
I see if I can do a benchmarking wheel with different parameters for each arm.

andreisperid, 2023-05-04:
From what I remember, Olivetti's daisywheels are made of some kind of composite plastic

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

From the bottom it is possible to see that perhaps it is not the flection of the teeth that make up for the flexibility, but that film itself. Of course, the type writer application is a bit different, because to transfer the tape pigment to the paper, a fast "hammering" is enough.

In the E-TKT's we are currently pressing to deform the tape, what creates the possibility of horizontal slipping.

But, on the other hand, if we have the flection enabled by that film, we could try increasing the teeth vertical thickness!

andreisperid, 2023-05-09:
Just dropping an idea that I had:

Instead of reproducing the design of the injected plastic daisywheel teeth, there could be some kind of spring to improve the flexibility between the core and the tips.

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

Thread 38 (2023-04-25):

Cancel label during print

andreisperid, 2023-04-25:
Now that we are just about to allow longer labels to be embossed, I got thinking that we might want to cancel it during print.

A flow would be something like this:
1 - user writes the label and hits print
2 - user desires to cancel, which happens after a modal confirmation (just in case)
3 - the device receives the instruction and finishes the process of embossing up to 1 letter
4 - the device feeds once, then cut
5 - idle and ready to receive new instructions

sabeechen, 2023-04-29:
My personal primary use case for wanting to cancel a print is when I mess something up (like forget to feed in tape, or set incorrect alignment values) and don't want the machine to just grind against itself for a while, in which case having a feed and cut defeats that objective somewhat.

The cancel your proposing (finish letter + feed + cut) is however probably more practically useful for most situations, and having an extra button just do do an "emergency stop" might clutter the UI.  Especially considering I can just push the physical reset button on the device when I mess something up.

I'd like to also propose then that this "controlled cancel":
 - Plays a sad short song as soon as its recieved.
 - Gets some indication on the oled, eg "Canceling label..."

Some care would need to be taken in the firmware for how the cancel is implemented, to ensure it doesn't cancel reboots, parameter saves, feeds, cuts, etc.  It should probably only ever cancel a normal label print.

andreisperid, 2023-05-01:
Good points.

From an interface point of view, I'd use a poka-yoke approach, meaning we shouldn't even be able to cancel what we shouldn't. Together with keeping all other buttons disabled during the cancel procedure, this might eliminate the problem of messing with reboots, saves, etc.

What we want to cancel (and only via web app, meaning it is a "soft cancel"):
- **printing label**: here we might want to finish the current letter, feed (maybe isn't needed at all) and cut (this is needed);
- **testing align/strength**: only stop where it is might do the trick, since its a testing procedure;

So, for each of them, when "in progress" there should appear an nested/overlaid button to the side of the button you used to start the command.

This controlled cancel procedure seems nice! We can use a sad trombone melody and sad emoji :P

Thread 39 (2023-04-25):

Synchronize label being printed through different devices

andreisperid, 2023-04-25:
Right now, if a label is sent to be printed in a device, and then a second device connects to the machine, the latter progress is shown based on whatever is written on the second input label (not the actual label being printed).

For instance, below a second device which had nothing written, while a printing was already been started prior. It misleads the user as if that placeholder text was being printed:
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

Any device should show the actual characters that are being printed, with its respective progress.

For that, perhaps the device should advertise the current label.

sabeechen, 2023-04-29:
I 100% agree, I can take this on as its something I've been planning to do ever since I json-ified the webserver.  Should be as simple as returning the current label as part of the status request and accurately rendering it in the web-app.  I'll also make sure it doesn't overwrite a label you're editing if a print starts in the middle of that.

sabeechen, 2023-04-29:
I've got a PR ready to go for this [in a branch](https://github.com/sabeechen/E-TKT/tree/label-webapp-sync), but it depends on the changes in my [OTA PR](https://github.com/andreisperid/E-TKT/pull/41), so I'll wait until that PR is reviewed (or rejected!) to request review.

andreisperid, 2023-05-01:
Amazing, thank you again @sabeechen !

And it is really nice that you made this parallel component to keep the previously written text 👏 #43

Closed 2023-05-01.

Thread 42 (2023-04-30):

Break up, refactor, and enforce style on the E-TKT firmware code

sabeechen, 2023-04-30:
I think it would be a good idea to refactor the E-TKT from its current (largely) single file structure into one that encapsulates its functionality into multiple classes.  There are many advantages to this, but the biggest I see are:
- Breaking functionality into smaller parts will make it easier to follow logic.
- Smaller files are easier to read, and therefore more maintainable.
- Breaking up functionality makes it easier to avoid conflicting changes if multiple people work on the project simultaneously.
- Bugs are less likely if the state for the device isn't all tangled together everywhere.
- Extending functionality is easier to do (ie for different hardware) when responsibilities are clearly defined by a class structure.
- Adding tests will be easier if most classes depend on abstractions of the hardware rather than the arduino methods themselves.

These are the typical upsides of breaking up and encapsulating functionality.  As usual it also comes with some downside, if things are broken up naively then it can often become more work to add functionality because the relationships between parts doesn't reflect what they actually need to do.  My goal would be to avoid that, and I think I'm familiar enough with the project to do it well.  I have a lot of professional experience doing this kind of thing, though not specifically with C++.

Here is how I'm initially thinking of breaking things up:
 - Printer.h - A "main" class created at the start which initializes everything and keeps track of global state like print progress, busy, etc
 - Helpers.h - Static utility methods, like the ones for handling utf-8 text.
 - Carousel.h  - Manages everything having to do with the carousel geometry, its stepper motor, and homing.
 - Sound.h - Manages making sounds/music with the buzzer.
 - Display.h - Manages all the logic for displaying info on the oled.
 - Server.h - Sets up the webserver, its callbacks, and passing info from requests to where they need to go.
 - WiFi.h - Handles the logic for connecting to WiFi, AP Config mode, mdns, etc.
 - Button.h, Light.h, Motor.h  - To handle smaller units of hardware.  These classes will probably be very simple.

While actually untangling the relationships whats needed might change, but I think its likely things will look close to this.

From my personal experience its better to make big changes like this quickly all at once to minimize the time it impacts people with pending changes.  Id want to break it all up quickly and coarsely in one PR, when go through and refactor/clean up individual classes by themselves at a more leisurely pace.

Alternative would be to check-in each new class one at a time, slowly carving out functionality from LabelMaker.cpp.  This is less disruptive to concurrent contributors but can take a lot longer to complete.

As things are broken up I'd like to move toward enforcing a C++ style, the most obvious choice is probably [Google C++ Style](https://google.github.io/styleguide/cppguide.html) with [clang](https://marketplace.visualstudio.com/items?itemName=xaver.clang-format), but any of the common alternatives would be fine so long as its adhered to, including something we make custom.  Most projects choose one of the well-known styles (Google, Microsoft, Mozilla, etc) and then just override rules as they see fit.

@andreisperid You have your finger on the pulse of whats going on with this project currently.  Do you think this is a good idea, and if so do you think now is a good time to do it?

andreisperid, 2023-05-01:
I think that's a great initiative, @sabeechen

From a roadmap point of view, these are the major things that might happen from now on:
- improvements on hardware, that might affect the firmware somehow
- bugfixes that might appear with new browser versions
- integration with other systems such as the Home Assistant, Matter, etc, which will probably talk to the Server.h
- forking into other similar projects (lets say a braille embossing machine? I'm thinking of it ;)

So, right now I understand the E-TKT's archetype is pretty solid, which means the approach you brought makes sense and will not prevent any development. Instead, it might even improve as collaboration will surely take advantage of that clear structure.

Also, for me it will be surely a great opportunity to learn, I'm looking forward to it! I trust whatever you bring ;)

skrutt, 2023-05-01:
Great idea, i agree! I would probably go for one piece at a time, simpler to get an overview and there are a lot of moving pieces.
Today the code is quite interleaved and many things rely on each other, for example the print progress is updated in a display function. Sort of makes sense since that functionality is available there but not is you are looking to create functional modules with clean, well defined interfaces.
Will be interesting to see where it goes, i would probably go for a function based layout instead (display, print, music, web), but both have merit.

If you do a music module, would you make that non-blocking? Cuz that would be cool 😄

sabeechen, 2023-05-02:
Yeah, its got some oddities.  But maybe it won't for much longer?
I made a proposal for my massive refactor in [this PR](https://github.com/andreisperid/E-TKT/pull/46).
Non-blocking execution is on my mind, but won't be in this change.  Its a tricky thing to get working in the device's state model but possible down the line.

andreisperid, 2023-05-04:
Implemented on #46

Closed 2023-05-04.

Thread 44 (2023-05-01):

Label cutting is erratic

andreisperid, 2023-05-01:
One of the things that never made me happy with the device is the cutting performance. Its still quite random.

What happens now:
- the machine presses three times to make sure the blade is able to pierce through both the label and liner;
- sometimes the labels are perfectly cut, sometimes not;
- eventually, there are white marks on the extremities, due to excessive press (energy is applied in the wrong place?);

Hypothesis:
- it seems that depending on the first cut, the label tilts a bit creating a better clearance for the next cut;
- maybe the label thickness varies, impacting performance;
- the blade gets dull (or comes with irregular sharpness?);
- the press might be hitting erratically, missing the ideal daisywheel spot;
- the homing might be imprecise, leading to the item before;
- the current servo might be enough for the characters, but not for cutting;

The ideal scenario would be:
- fully cut the label, but leave just a tiny bit of liner uncut to make sure the label isn't carried by the daisywheel and get entangled;
- prevent damaging the tape (white marks);
- make sure the little tab (double cut) is functional to help removing the liner, which means fully cutting the external (except tiny bit of liner), but for the inner, only cut the label, but not the liner;
- press only once to cut;

sabeechen, 2023-05-03:
I have a few ideas, though I also wonder if just one cut might be enough.  I've grown rather fond of the little pre-cut tab that sometimes forms, it makes getting the backing off *really really cheap* label tape easier.  I suspect the mechanics of the cutting is actually very chaotic.

My best guess about what causes the displacement during sequential cuts that should be in the same place is slack in the channel that the label runs through, since the label tape wants to curl after it comes off the tape.  I'll attempt to describe my theory with crude drawings:
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
Before a cut, viewed from the side, the tape forms one solid arc back toward the feeder.  After the first press on the cutter the kink allows the tape to form two more shallow arcs, which covers the same horizontal distance with less tape, causing a slight shift where the next cut takes places.  The cut itself will also definitely cause the tape to stretch a little as the tape squeezes out the sides of the blade, also causing some displacement.  I suspect that the tape doesn't always have a lot of slack/arc, which is what makes the subsequent cuts only sometimes land on a different spot.

Some ideas I have to have solve this, though they'd all take some experimentation to get right or even prove worthwhile:
1. Instead of fully returning the press to its rest position for each cut, only back off slightly so some tension is left on the tape keeping it in position.  Subsequent cuts would then kind of "chew" through the tape without fully releasing it.
2. Only do one cut, but while the press is still raised pull back slightly with the feed stepper.  Pulling back might help encourage the tape to tear in the right place without too much collateral damage to the edges.  It might even be worthwhile to move the tape back and forth a little.
3. If the displacement in subsequent cuts could be characterized somehow, the feed motor could feed/retract the correct amount between cuts to get the tape to land in the right spot.

All of these could even be combined together to make the E-TKT do a grindy little dance during a cut.  Though it may also be the case I'm way off base and none of this would help.

andreisperid, 2023-05-03:
Great observation and ideas. I like very much the bite-chew, and also the bite-tear.

To avoid missing steps that might occur in the latter, maybe we can even reduce the acceleration to raise the torque.

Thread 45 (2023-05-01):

Hall sensor directly on the PCB

andreisperid, 2023-05-01:
Instead of using an independent breakout (keyes ky 003), the PCB could directly hold the hall sensor with an SMD form factor.

This could help with:
- more solid positioning to avoid later homing calibration issues;
- avoid usage of different hall sensor specs (44E 402 *vs*  3144) populated in the same ky 003 module, which have completely different sensor outputs when exposed to the magnetic field;
- simpler pillar piece;
- much easier assembly and less screws;

That would impact:
- PCB: would encompass the sensor (but SMD), a resistor and a LED that are currently in the breakout;
- F_pillar;
- I_nema_wheel_hub: would need to bring the magnet closer to the PCB, without colliding with the P_press;

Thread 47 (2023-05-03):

Ease wi-fi connection by using push-button WPS

andreisperid, 2023-05-03:
The device has got two switch buttons that could be used to facilitate the wi-fi configuration by using push-button [WPS](https://en.wikipedia.org/wiki/Wi-Fi_Protected_Setup):
- FN: only used to enter the bootloader mode
- Wi-fi: used to clear the wi-fi settings if pressed during the boot, but not using for anything else.

The second one seems more suitable for the purpose and the label already placed. Ideally, there should be a dedicated WPS button to avoid confusion.

So instead of entering the device's captive portal and inserting the SSID and password, the user could simply auto configure by pressing a button on both the device and the wi-fi router.

This [example ](https://github.com/espressif/arduino-esp32/blob/master/libraries/WiFi/examples/WPS/WPS.ino) seems to have potential, but I didn't analyze it in depth yet.

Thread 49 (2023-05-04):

Implement LEDs using ledc method

andreisperid, 2023-05-04:
As [commented](https://github.com/andreisperid/E-TKT/pull/46#issuecomment-1535059715), currently the LEDs (ledChar and ledFinish) are using analogWrite, which are by convenience supplied by the ESP32Servo library. This might be bad for modularity in case another library is used, or any changes in the architecture are made.

And, maybe there are other opportunities by using this official method.

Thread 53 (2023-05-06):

NEMA for better feeding

andreisperid, 2023-05-06:
Instead of the small 28BYJ, a NEMA stepper motor could be used to increase the feed speed, precision and reliability.

Since there is no need to use both the char and feed at the same time, I had the idea of having a single A4988 driver to control both via switching. With that, the ULN2003 could be eliminated.

The down point is that a major structure redesign should be made, since the NEMA is way bigger.

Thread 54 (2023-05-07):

Add support for Trinamic drivers

sedorr, 2023-05-07:
Maybe add support for StallGuard4 and StealthChop2 via the TMC2209. It should be relatively easy since you already use the standard driver modules used in 3d printers.
If you don’t need stall detection the TMC2208 should even be a drop in replacement for the A4988 (in legacy mode at least as far as I know).

andreisperid, 2023-05-08:
Pretty cool, nice idea. I've been interested on experimenting with the TMC2209 for sometime.

By quickly looking in the [datasheet](https://www.trinamic.com/fileadmin/assets/Products/ICs_Documents/TMC2209_datasheet_rev1.08.pdf), it seems that an UART port is needed to fully configure it, so maybe we can implement it with the next version.

Didn't know, but there is a way to use a sensorless homing, but unfortunately it is not compatible with the E-TKT. It needs a physical stop to detect home.

sedorr, 2023-05-08:
Maybe even consider doing away with the stepstick boards and solder a TMC2209-LA (or two) to the board.

If you don’t need stall detection the TMC2208 should be a drop in replacement for the A4988 (in legacy mode at least as far as I know). On the 2208 the UART is used for advanced stuff like full 256 microstep control and hybrid switching betwean stealthchop and spreadcycle mode. But you don't need it if you only need stealthchop and max. 16 microsteps you can get away without the UART.

sabeechen, 2023-06-23:
I tried swapping in a TMC2208, it is indeed a drop-in replacement for the A4988.  It seems to work the same, except I had to reverse the stepper direction in the firmware.  For anyone else doing it id recommend getting one preconfigured to disable UART mode, since its really difficult to move the config SMD resistor without a microscope, especially if the pin headers are already soldered.

The biggest difference is that the motor is nearly silent when moving (except for plastic rubbing on plastic) and the motor whine when holding position is gone.  I rather like it.

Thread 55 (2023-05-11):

Screws longer than needed

sedorr, 2023-05-11:
Most M3 20mm could probably be replaced with at least 16mm screws. As I already mentioned in [issue 29](https://github.com/andreisperid/E-TKT/issues/29), 2,5*(outer thread diameter) screw-in depth is theoretically enough. 20mm are quite long and tedious to screw in.

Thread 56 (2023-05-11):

Make screw holes tighter

sedorr, 2023-05-11:
I don’t have my pc with me right now so I can’t check what the screw hole diameter of the models is, but on my parts I had quite a lot of screws spinning freely in the hole.
It might just be a tolerance issue with my printer, but maybe consider adding a version with 2,5mm diameter holes that the user can then cut a thread into.

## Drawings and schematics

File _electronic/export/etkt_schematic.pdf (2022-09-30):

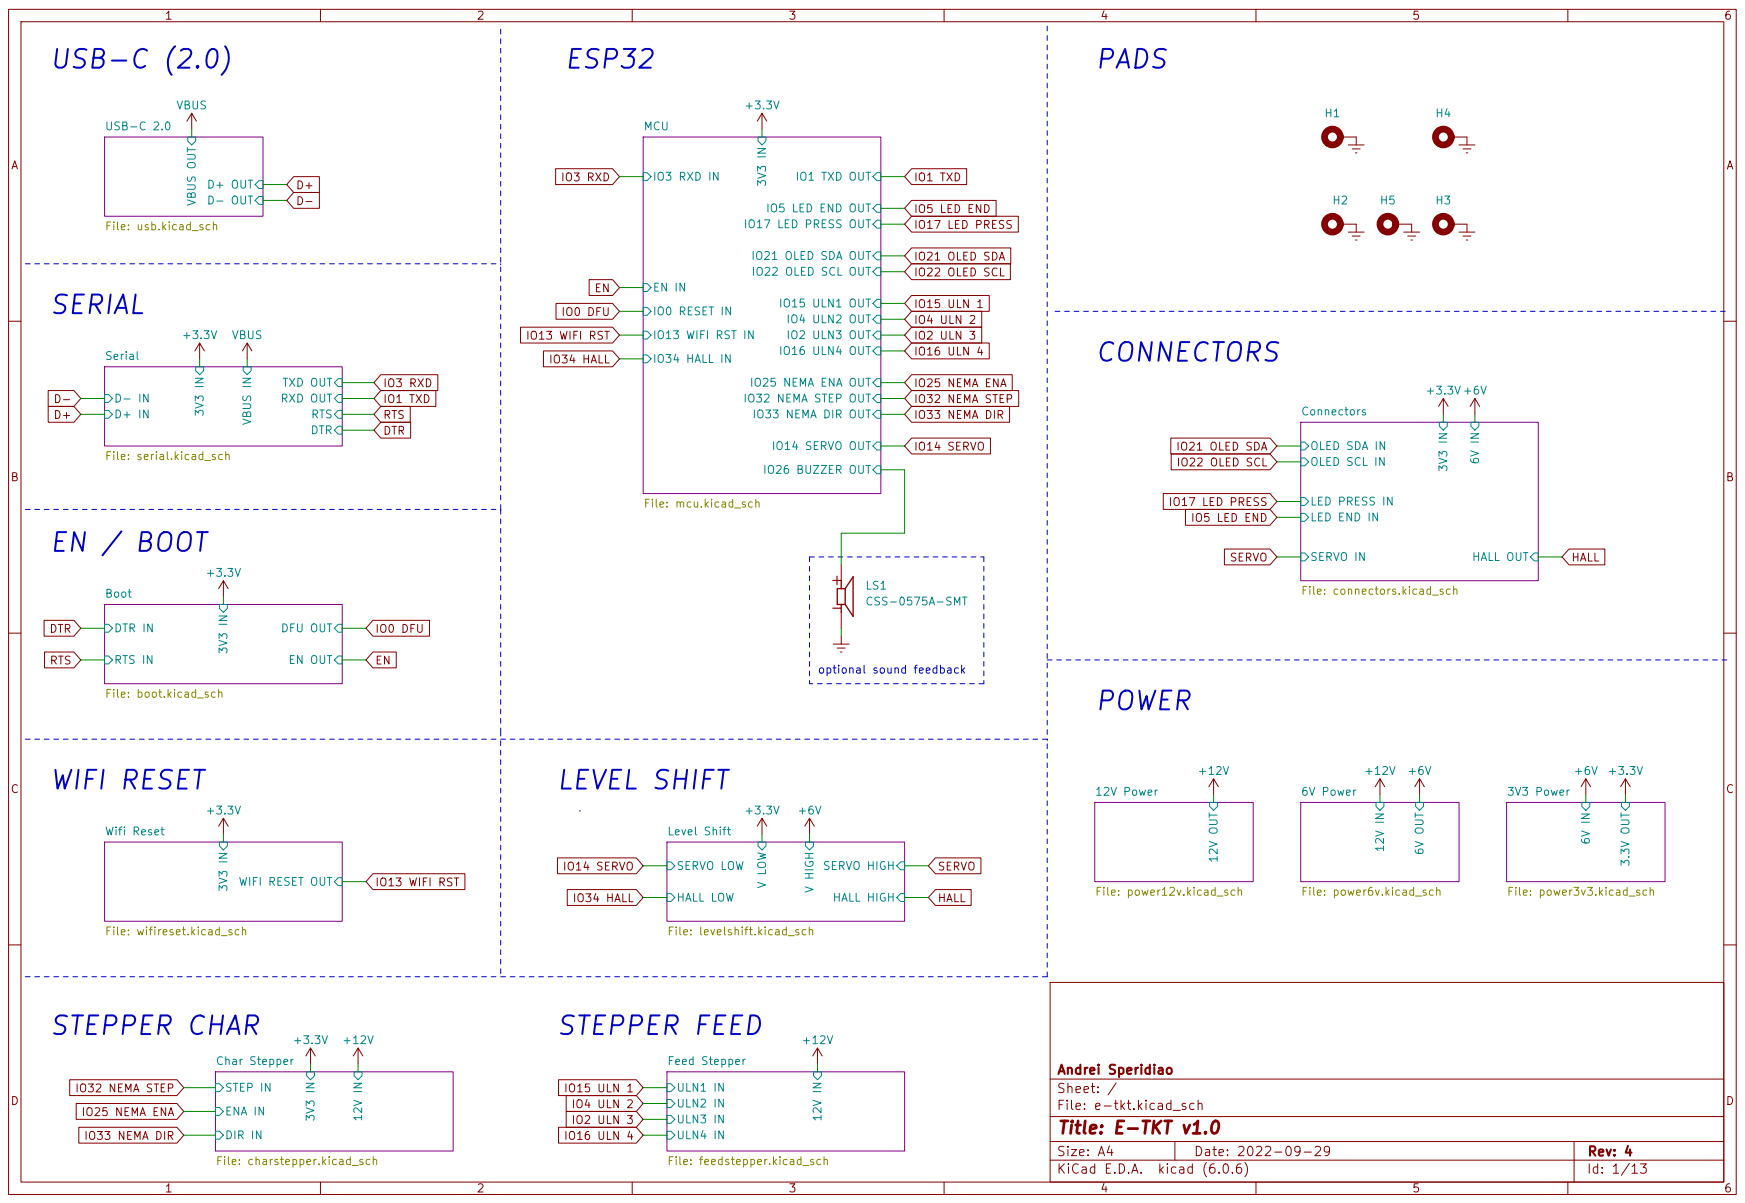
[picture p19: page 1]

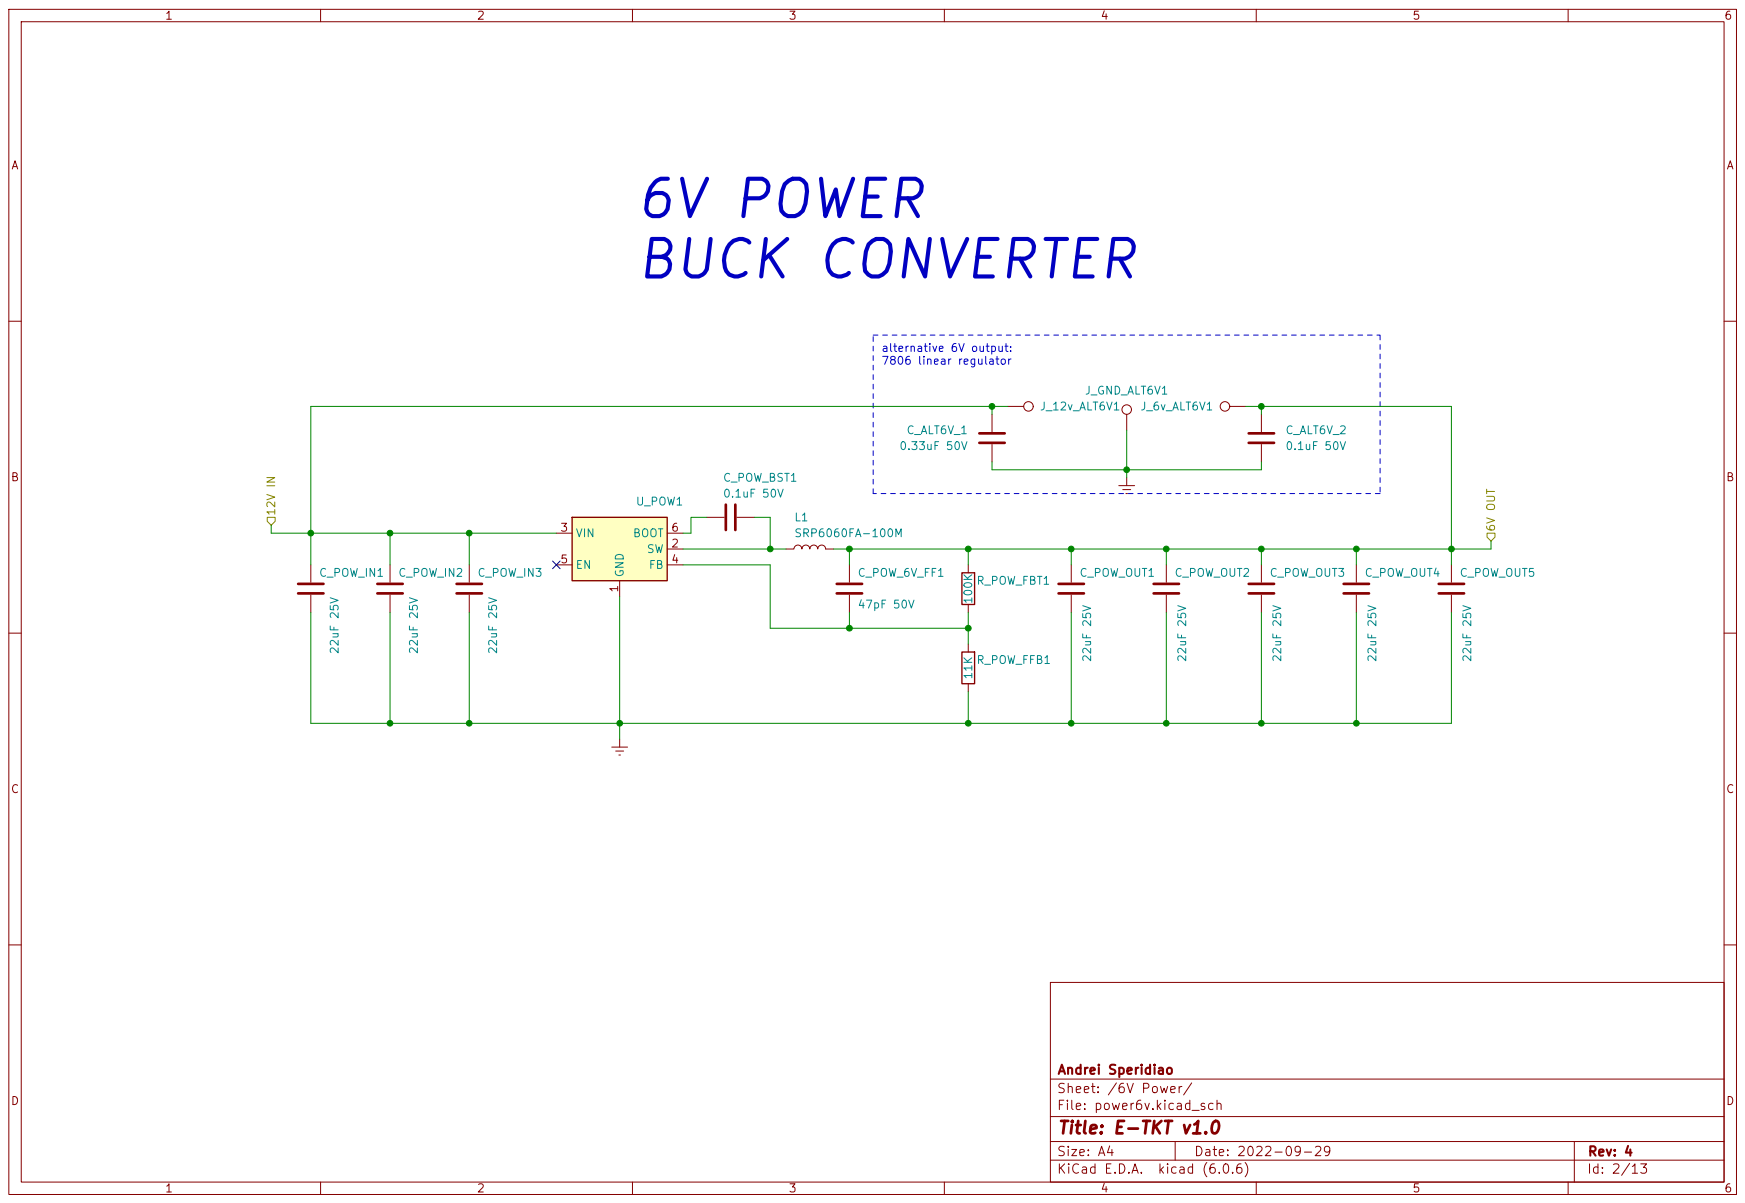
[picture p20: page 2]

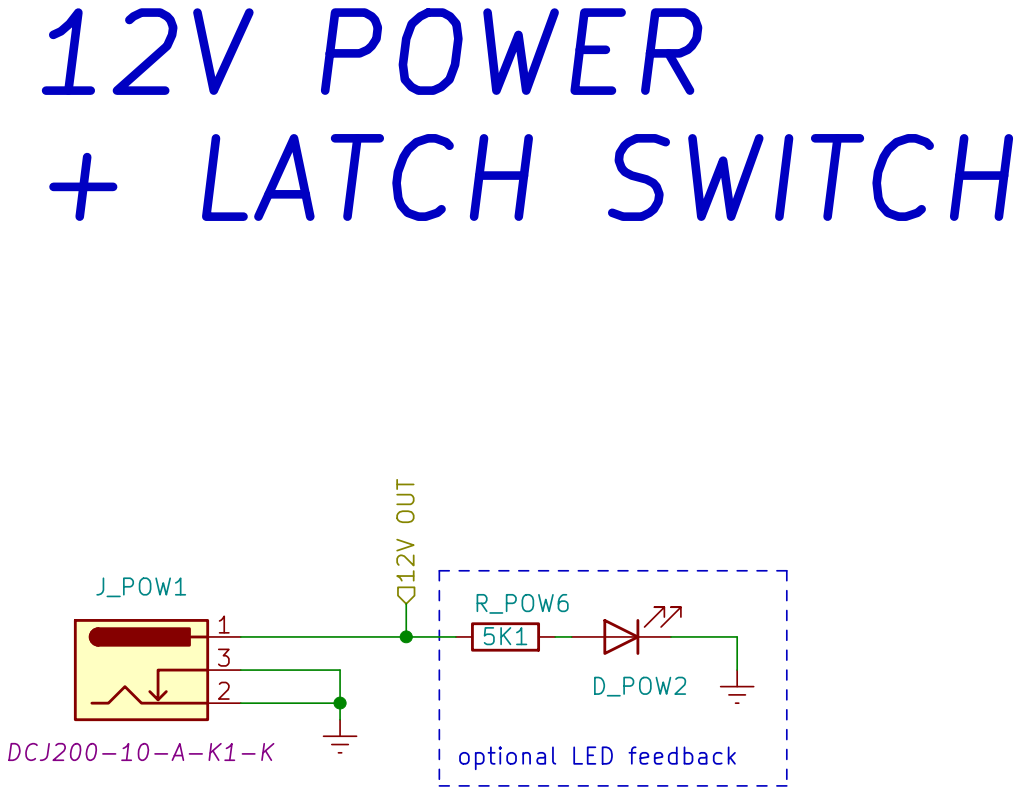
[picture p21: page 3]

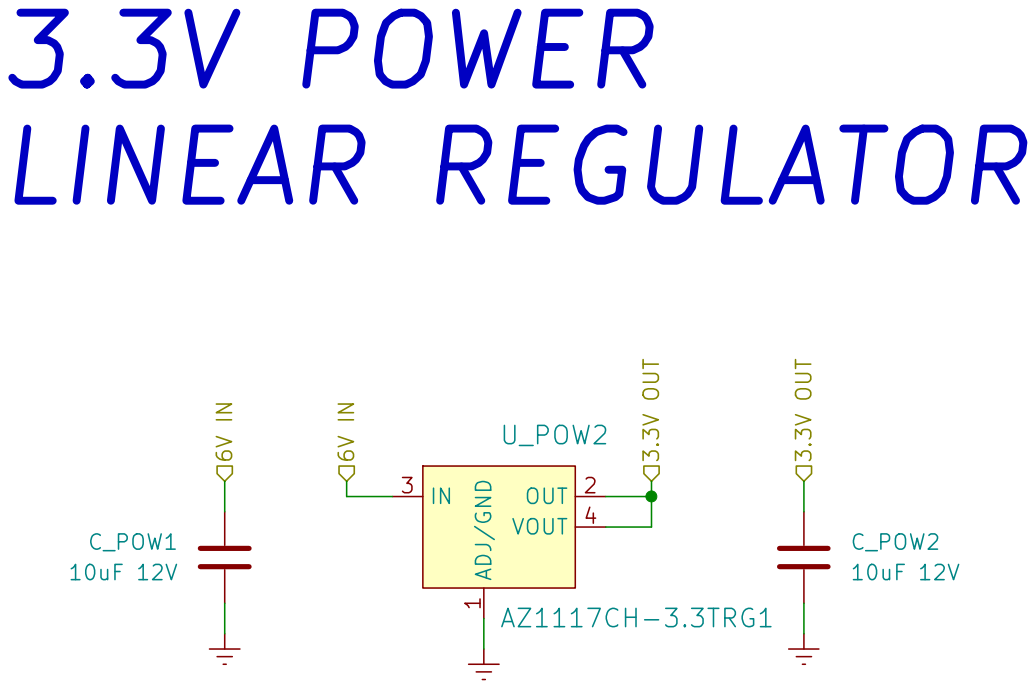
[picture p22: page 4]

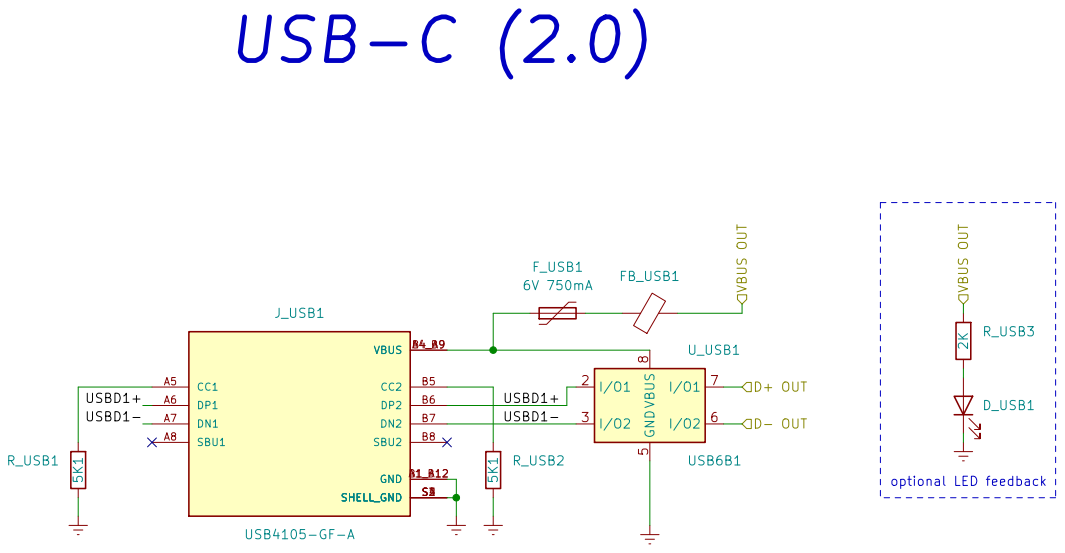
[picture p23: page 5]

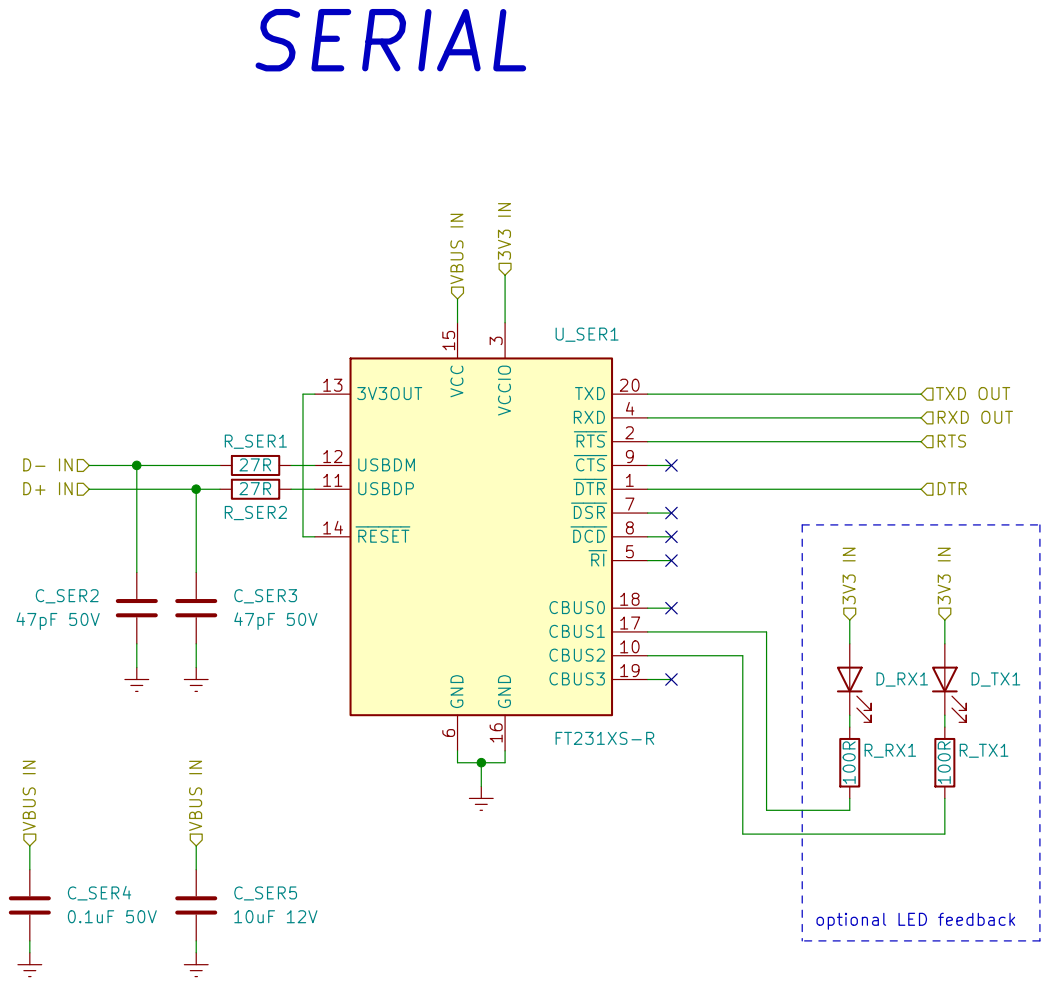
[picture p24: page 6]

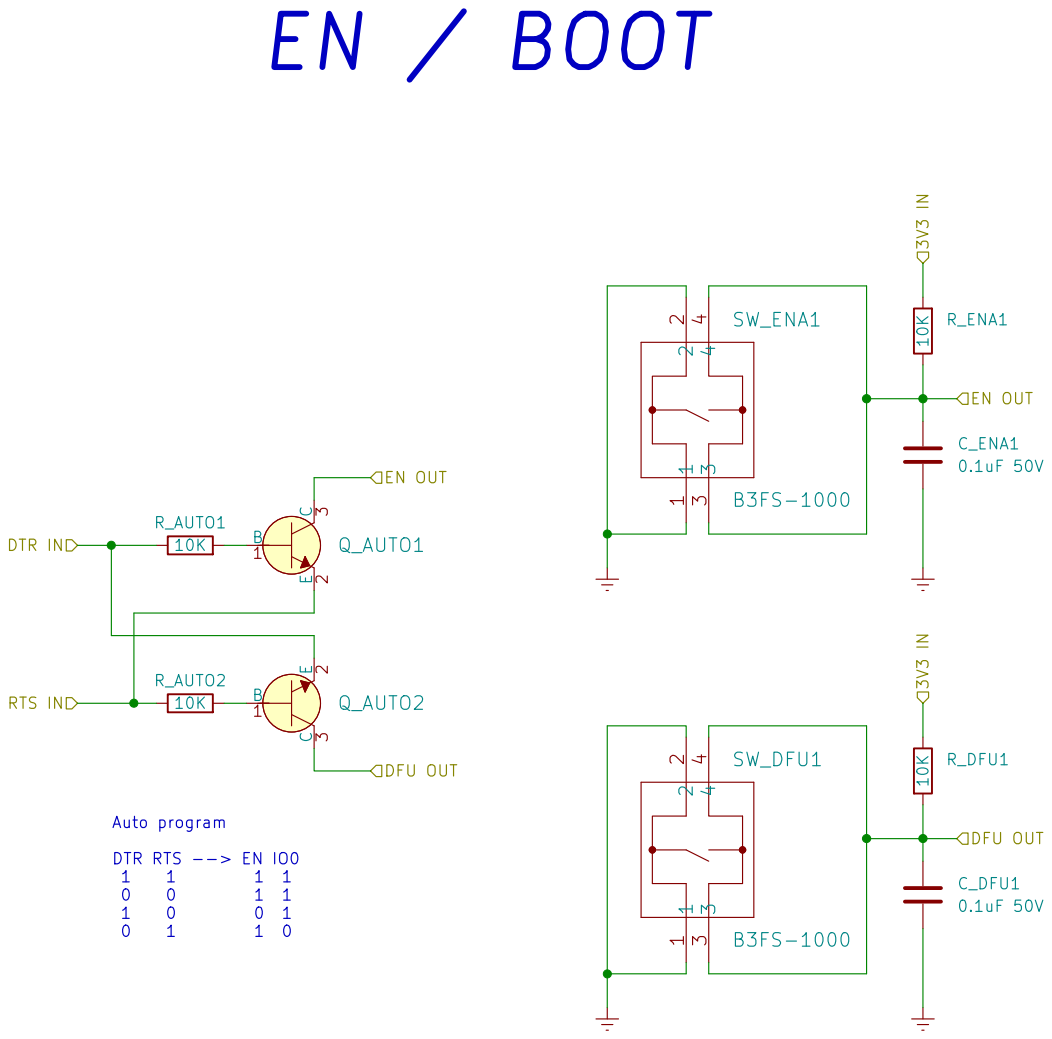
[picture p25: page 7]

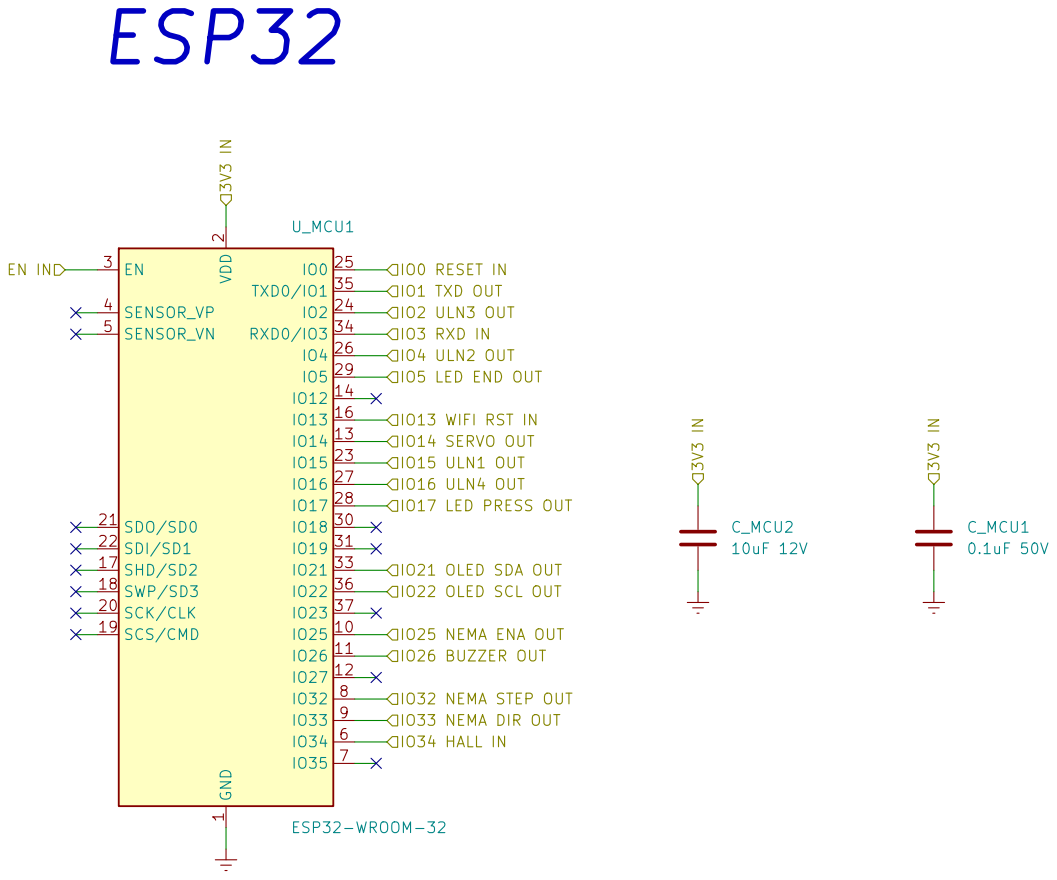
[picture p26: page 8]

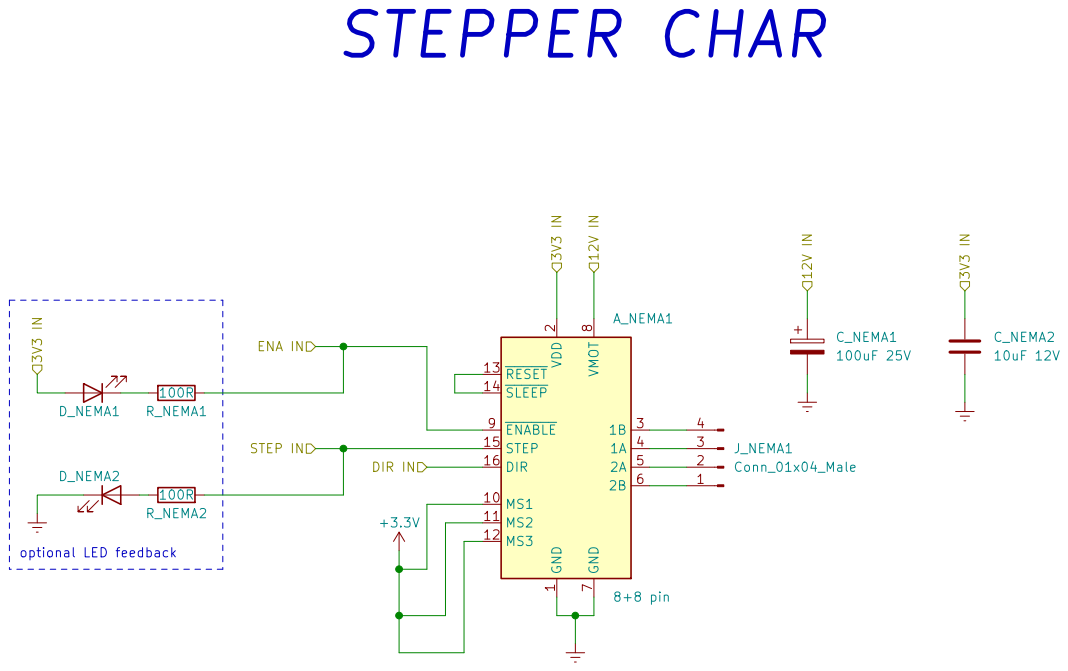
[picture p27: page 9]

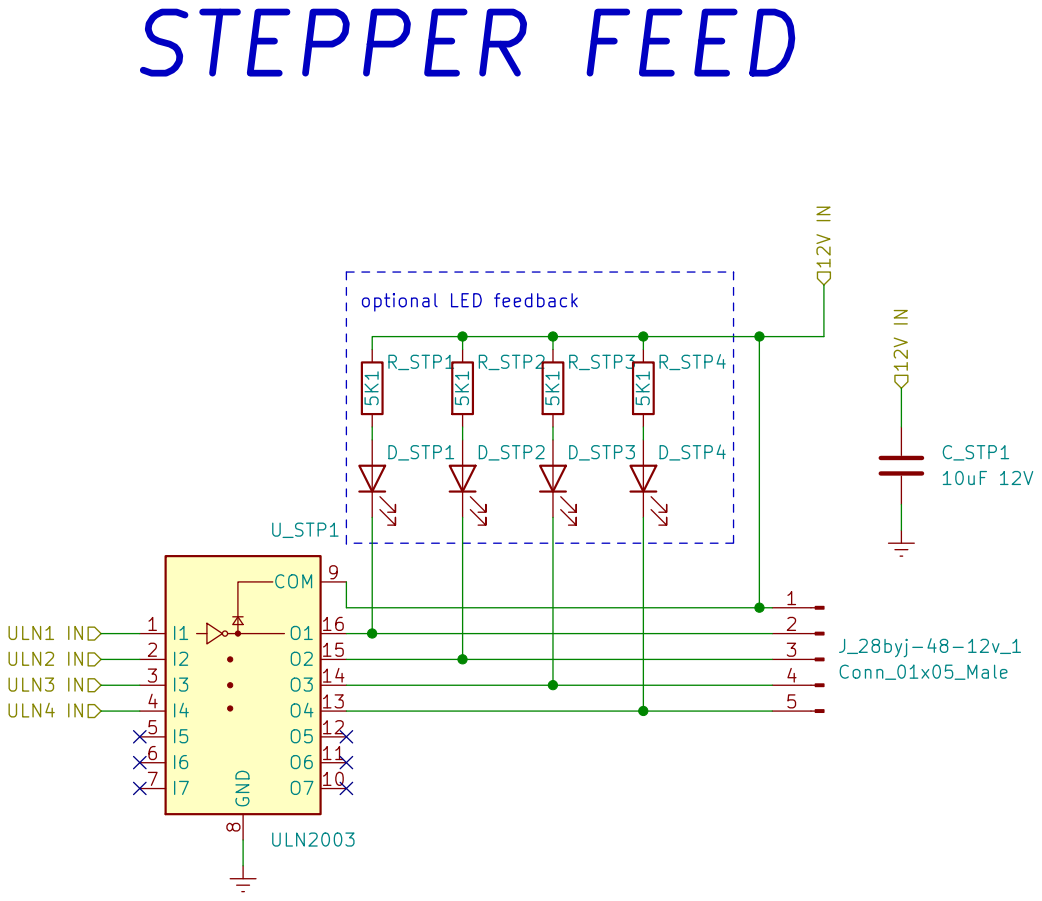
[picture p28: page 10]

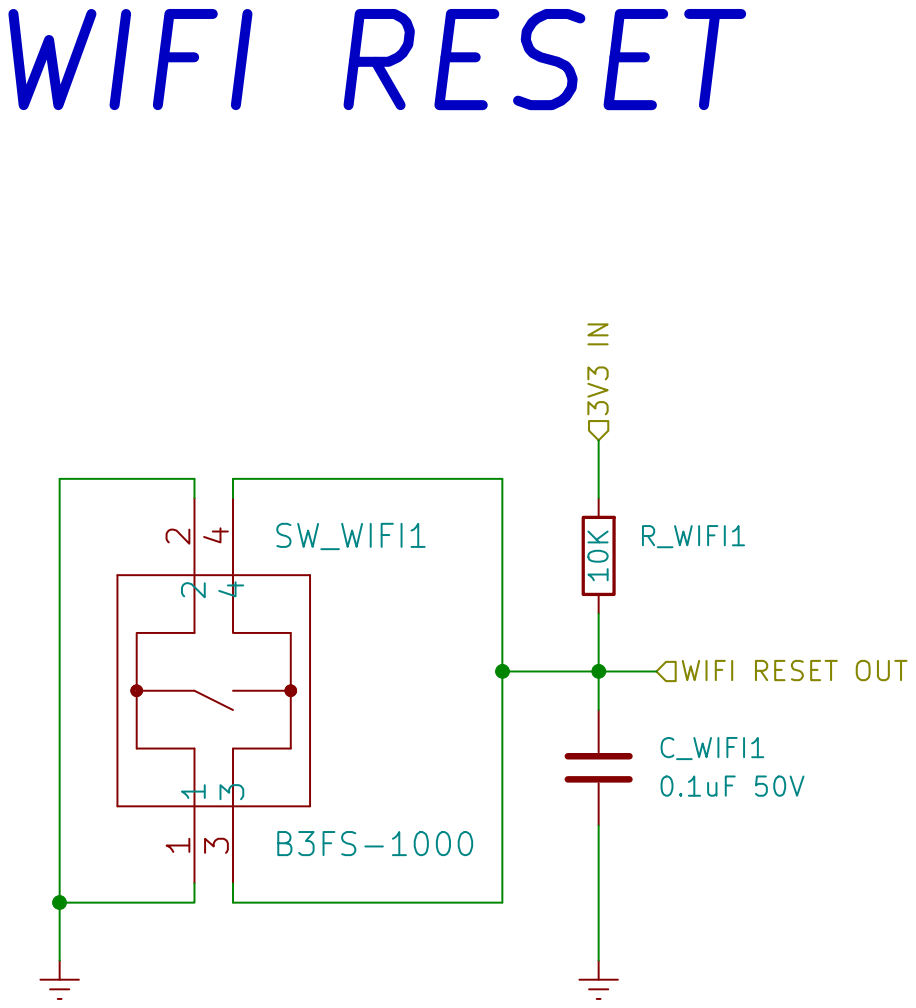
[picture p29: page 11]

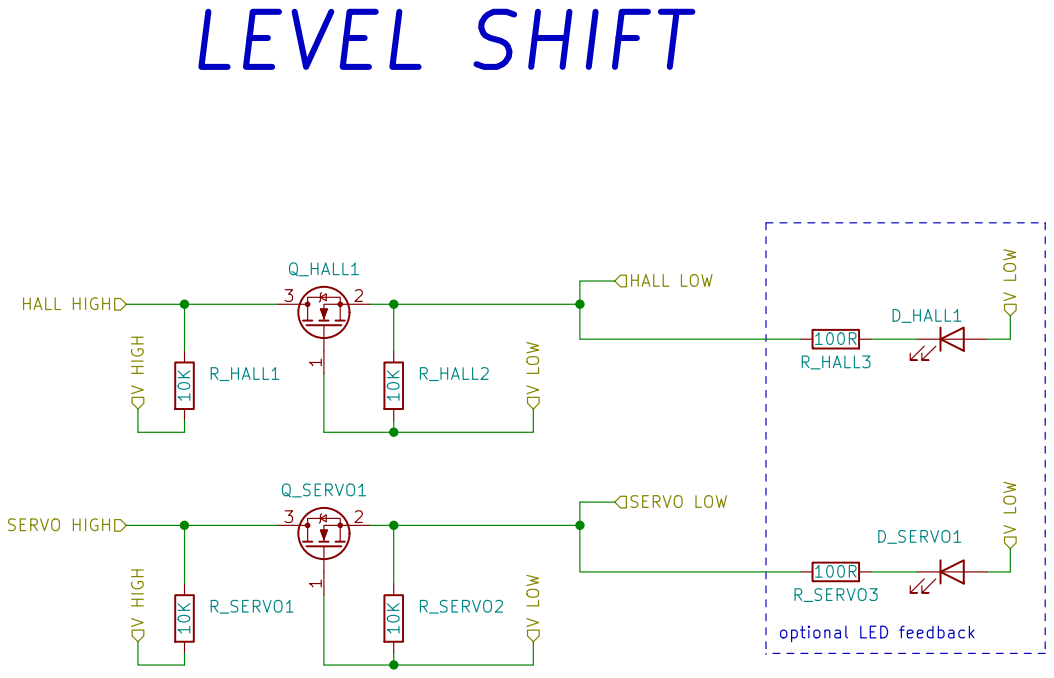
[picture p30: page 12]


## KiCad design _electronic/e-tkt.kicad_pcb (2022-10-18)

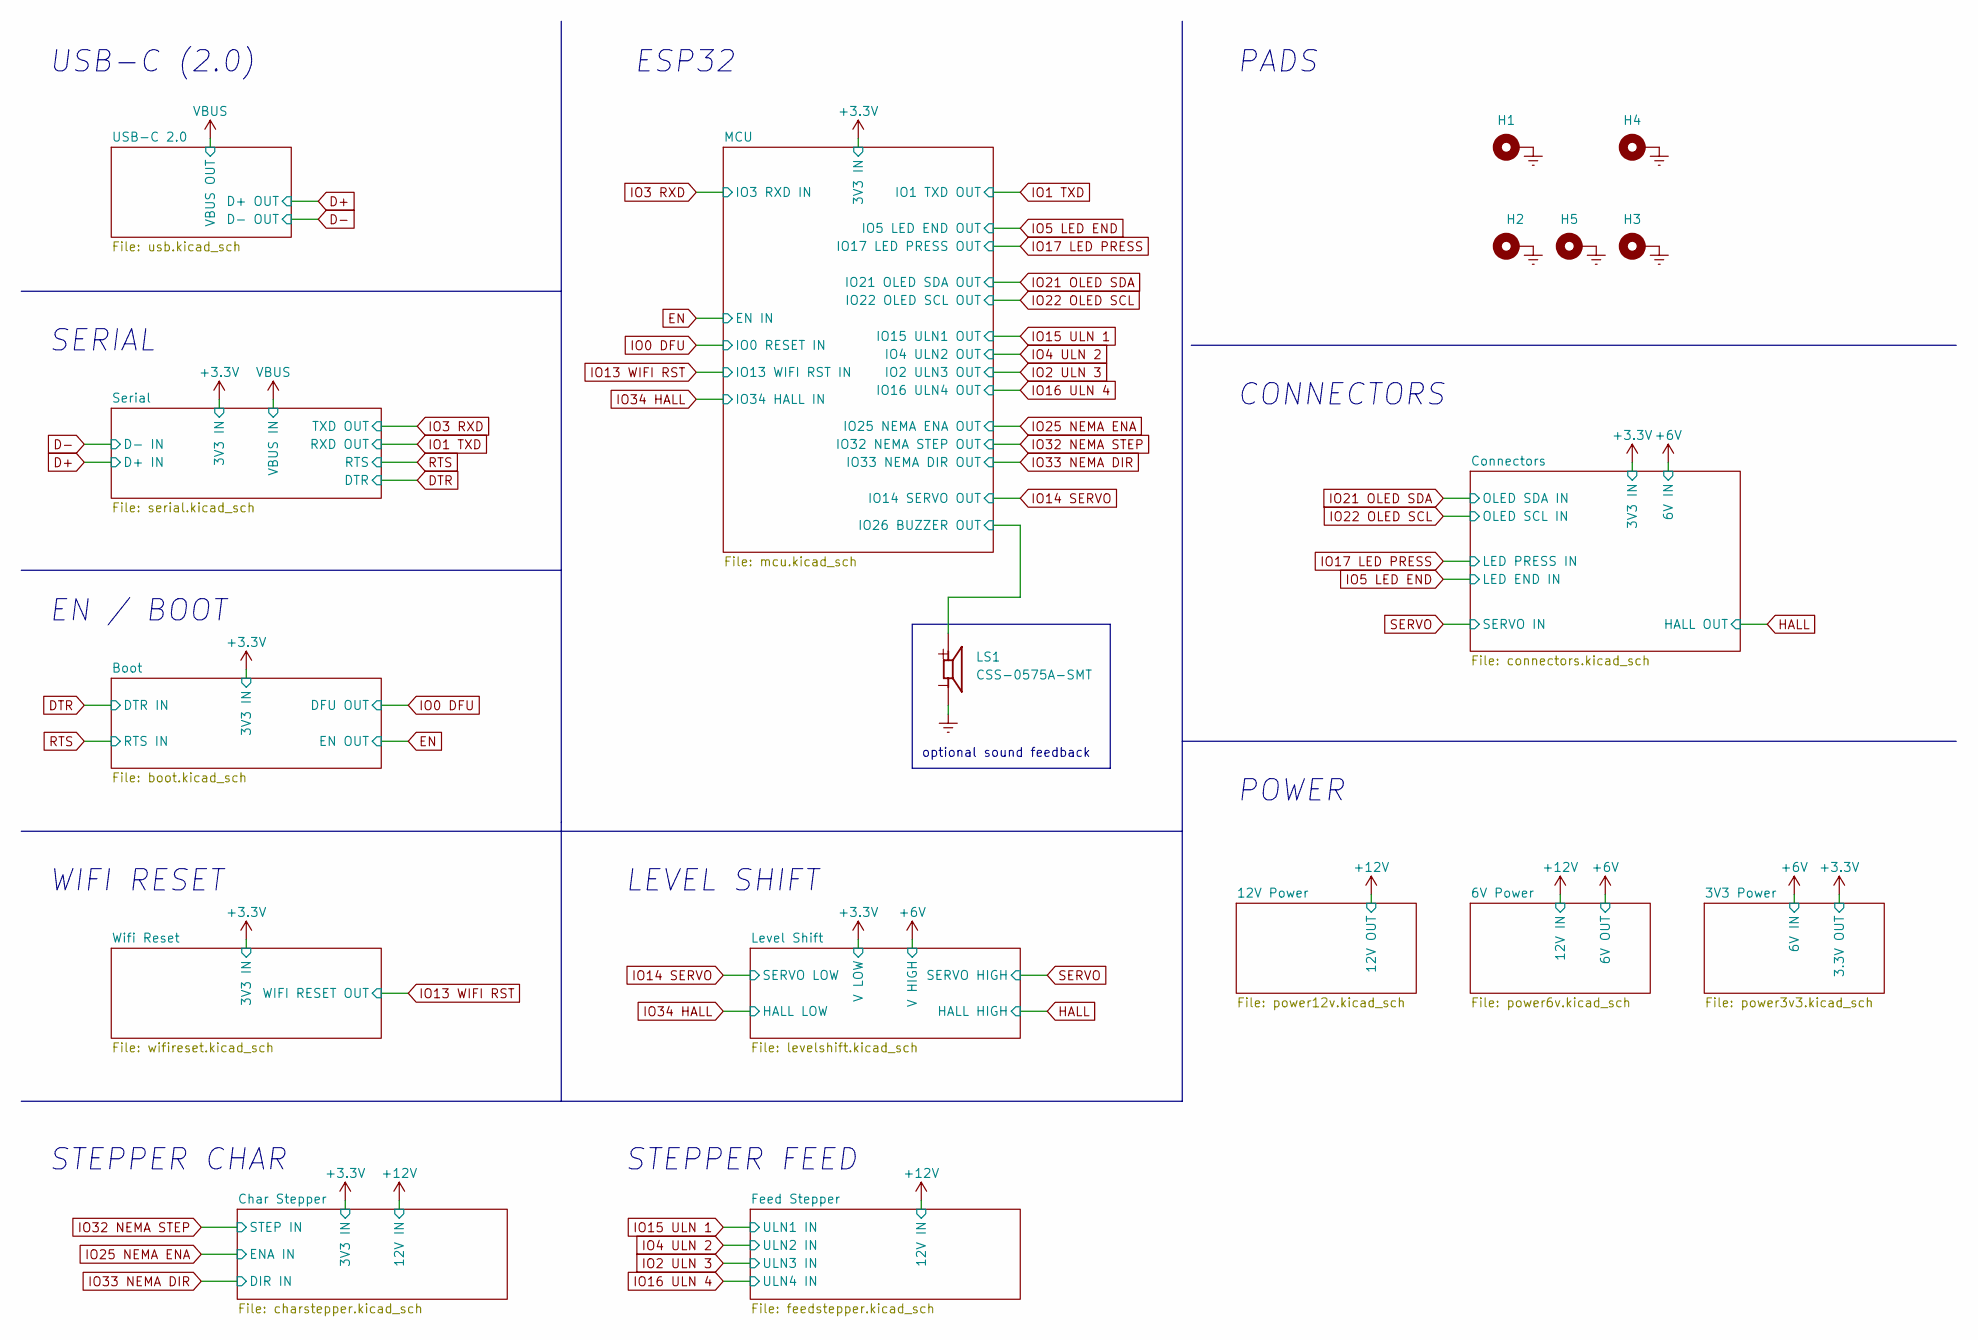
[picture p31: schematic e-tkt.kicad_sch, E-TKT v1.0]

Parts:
H1, H2, H3, H4, H5: M3; MountingHole_3.2mm_M3_Pad_Via; Mouser OK
LS1: CSS-0575A-SMT; CUI_CSS-0575A-SMT; Mouser OK

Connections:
/MCU/IO26 BUZZER OUT: LS1.1; also elsewhere on the board

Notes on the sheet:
PADS
POWER
optional sound feedback
SERIAL
EN / BOOT
CONNECTORS
STEPPER CHAR
WIFI RESET
ESP32
LEVEL SHIFT
STEPPER FEED
USB-C (2.0)

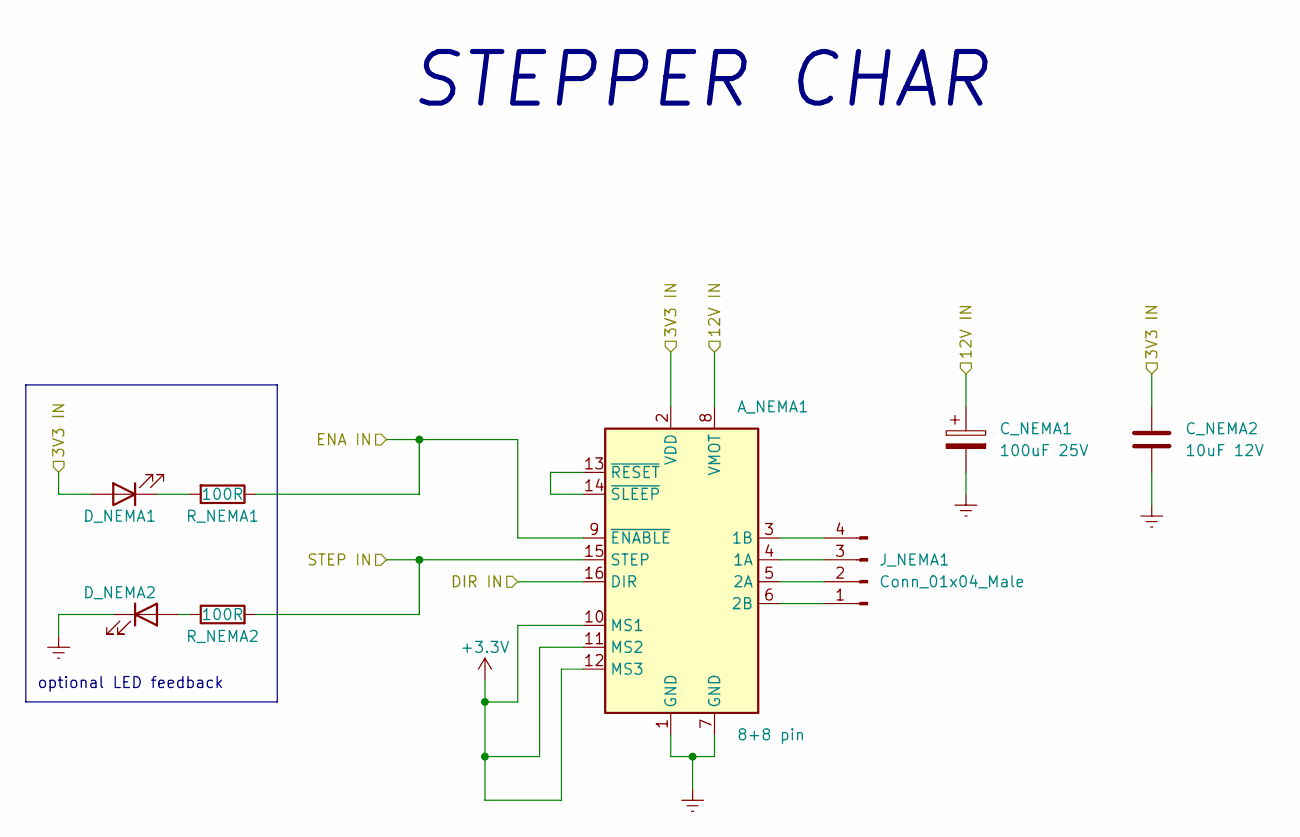
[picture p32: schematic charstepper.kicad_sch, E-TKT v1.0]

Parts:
A_NEMA1: 8+8 pin; Pololu_Breakout-16_15.2x20.3mm; Mouser OK
C_NEMA1: 100uF 25V; CP_Elec_6.3x7.7; Mouser OK
C_NEMA2: 10uF 12V; C_0603_1608Metric_Pad1.08x0.95mm_HandSolder; Mouser OK
D_NEMA1, D_NEMA2: LED white; LED_0603_1608Metric_Pad1.05x0.95mm_HandSolder; Mouser OK
J_NEMA1: Conn_01x04_Male; PinHeader_1x04_P2.54mm_Horizontal; Mouser OK
R_NEMA1, R_NEMA2: 100R; R_0603_1608Metric_Pad0.98x0.95mm_HandSolder; Mouser OK

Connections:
+3.3V: A_NEMA1.2 (VDD), A_NEMA1.10 (MS1), A_NEMA1.11 (MS2), A_NEMA1.12 (MS3), C_NEMA2.2, D_NEMA1.2 (A); also elsewhere on the board
+12V: A_NEMA1.8 (VMOT), C_NEMA1.1; also elsewhere on the board
IO25 NEMA ENA: A_NEMA1.9 (~ENABLE), R_NEMA1.1; also elsewhere on the board
IO32 NEMA STEP: A_NEMA1.15 (STEP), R_NEMA2.2; also elsewhere on the board
IO33 NEMA DIR: A_NEMA1.16 (DIR); also elsewhere on the board
unnamed: A_NEMA1.3 (1B), J_NEMA1.4
unnamed: A_NEMA1.4 (1A), J_NEMA1.3
unnamed: A_NEMA1.5 (2A), J_NEMA1.2
unnamed: A_NEMA1.6 (2B), J_NEMA1.1
unnamed: A_NEMA1.13 (~RESET), A_NEMA1.14 (~SLEEP)
unnamed: D_NEMA1.1 (K), R_NEMA1.2
unnamed: D_NEMA2.2 (A), R_NEMA2.1

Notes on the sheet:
optional LED feedback
STEPPER CHAR

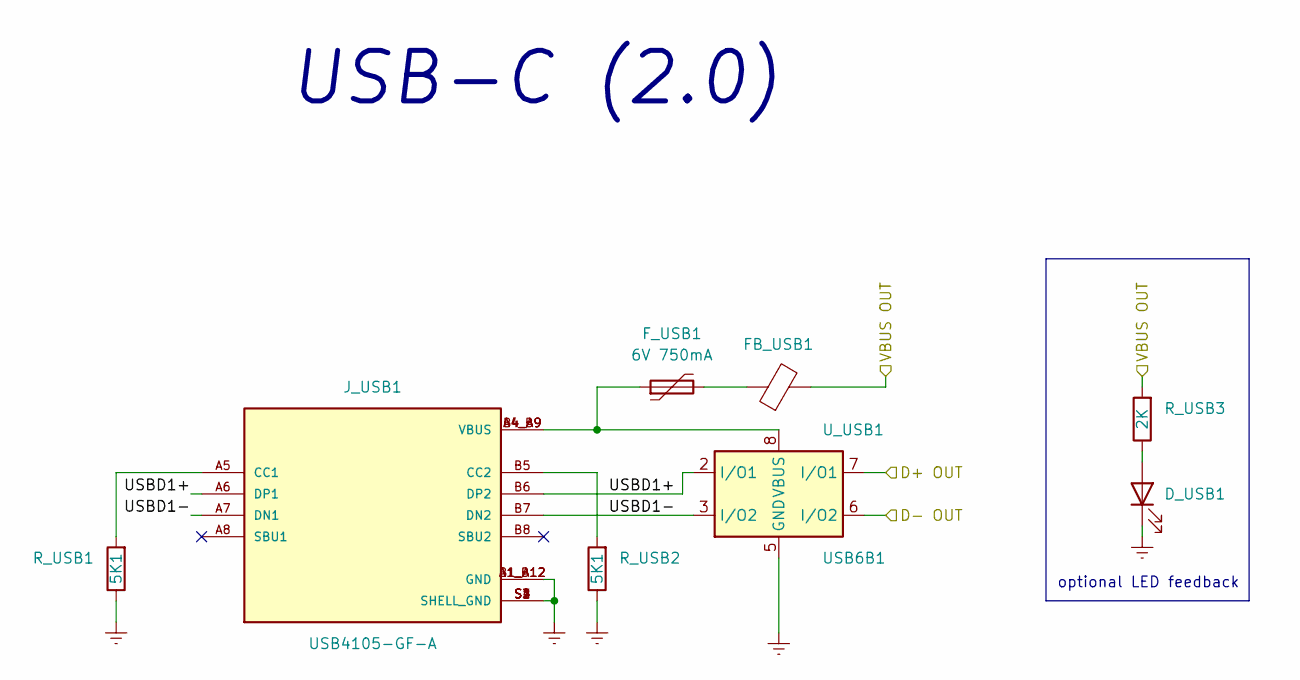
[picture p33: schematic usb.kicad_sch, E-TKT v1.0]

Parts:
D_USB1: LED white; LED_0603_1608Metric_Pad1.05x0.95mm_HandSolder; Mouser OK
FB_USB1: 40 Ohms @ 100 MHz 1 Power; L_0805_2012Metric_Pad1.05x1.20mm_HandSolder; Mouser OK
F_USB1: 6V 750mA; Fuse_0805_2012Metric_Pad1.15x1.40mm_HandSolder; Mouser OK
J_USB1: USB4105-GF-A; GCT_USB4105-GF-A; Mouser OK
R_USB1, R_USB2: 5K1; R_0603_1608Metric_Pad0.98x0.95mm_HandSolder; Mouser OK
R_USB3: 2K; R_0603_1608Metric_Pad0.98x0.95mm_HandSolder; Mouser OK
U_USB1: USB6B1; SOIC-8_3.9x4.9mm_P1.27mm; Mouser OK

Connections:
/USB-C 2.0/USBD1+: J_USB1.A6 (DP1), J_USB1.B6 (DP2), U_USB1.2 (I/O1)
/USB-C 2.0/USBD1-: J_USB1.A7 (DN1), J_USB1.B7 (DN2), U_USB1.3 (I/O2)
D+: U_USB1.7 (I/O1); also elsewhere on the board
D-: U_USB1.6 (I/O2); also elsewhere on the board
unnamed: D_USB1.2 (A), R_USB3.1
unnamed: FB_USB1.1, F_USB1.2
unnamed: F_USB1.1, J_USB1.A4_B9 (VBUS), J_USB1.B4_A9 (VBUS), U_USB1.1 (VBUS), U_USB1.8 (VBUS)
unnamed: J_USB1.A5 (CC1), R_USB1.2
unnamed: J_USB1.B5 (CC2), R_USB2.2
VBUS: FB_USB1.2, R_USB3.2; also elsewhere on the board

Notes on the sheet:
USB-C (2.0)
optional LED feedback

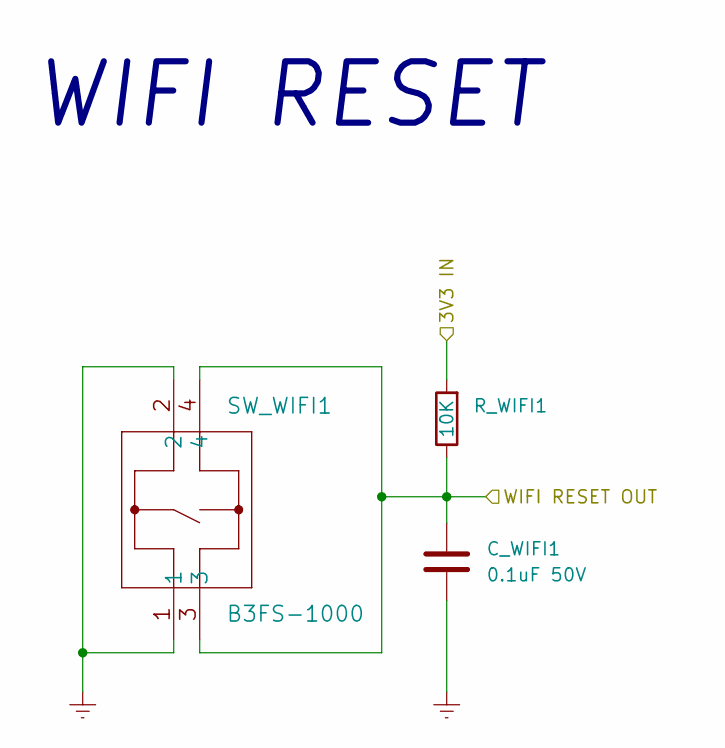
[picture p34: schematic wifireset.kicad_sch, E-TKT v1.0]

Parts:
C_WIFI1: 0.1uF 50V; C_0603_1608Metric_Pad1.08x0.95mm_HandSolder; Mouser OK
R_WIFI1: 10K; R_0603_1608Metric_Pad0.98x0.95mm_HandSolder; Mouser OK
SW_WIFI1: B3FS-1000; Mouser OK

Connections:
+3.3V: R_WIFI1.2; also elsewhere on the board
IO13 WIFI RST: C_WIFI1.2, R_WIFI1.1, SW_WIFI1.3, SW_WIFI1.4; also elsewhere on the board

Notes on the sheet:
WIFI RESET

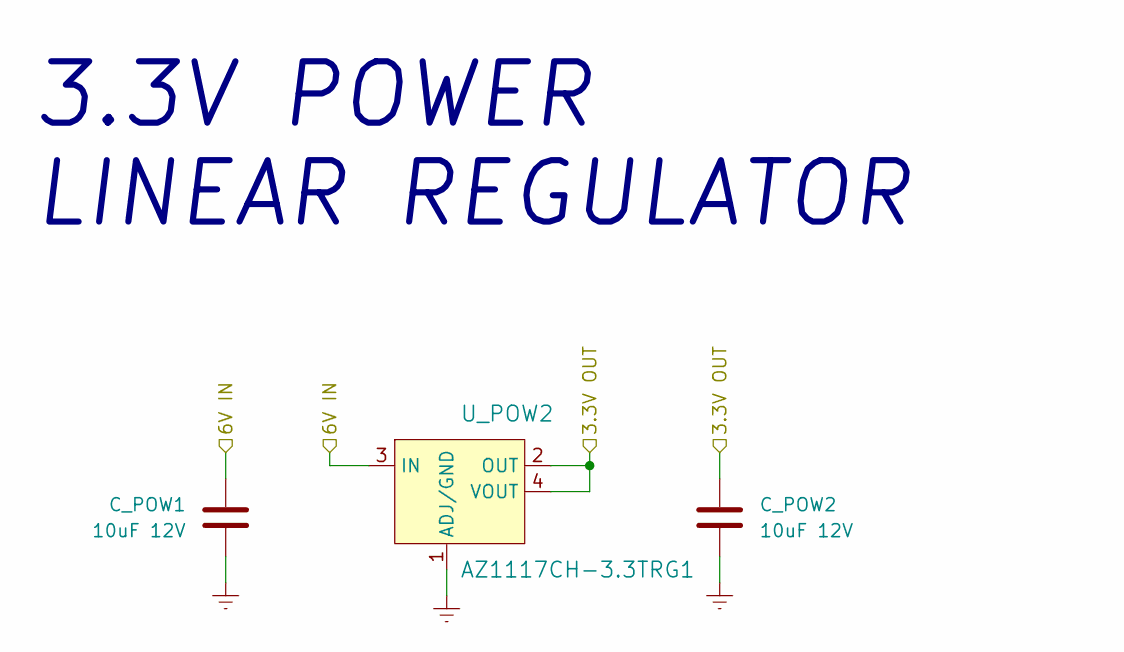
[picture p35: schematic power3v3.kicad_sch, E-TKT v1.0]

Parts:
C_POW1, C_POW2: 10uF 12V; C_0603_1608Metric_Pad1.08x0.95mm_HandSolder; Mouser OK
U_POW2: AZ1117CH-3.3TRG1; SOT-223; Mouser OK

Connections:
+3.3V: C_POW2.1, U_POW2.2 (OUT), U_POW2.4 (VOUT); also elsewhere on the board
+6V: C_POW1.1, U_POW2.3 (IN); also elsewhere on the board

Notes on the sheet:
3.3V POWER LINEAR REGULATOR

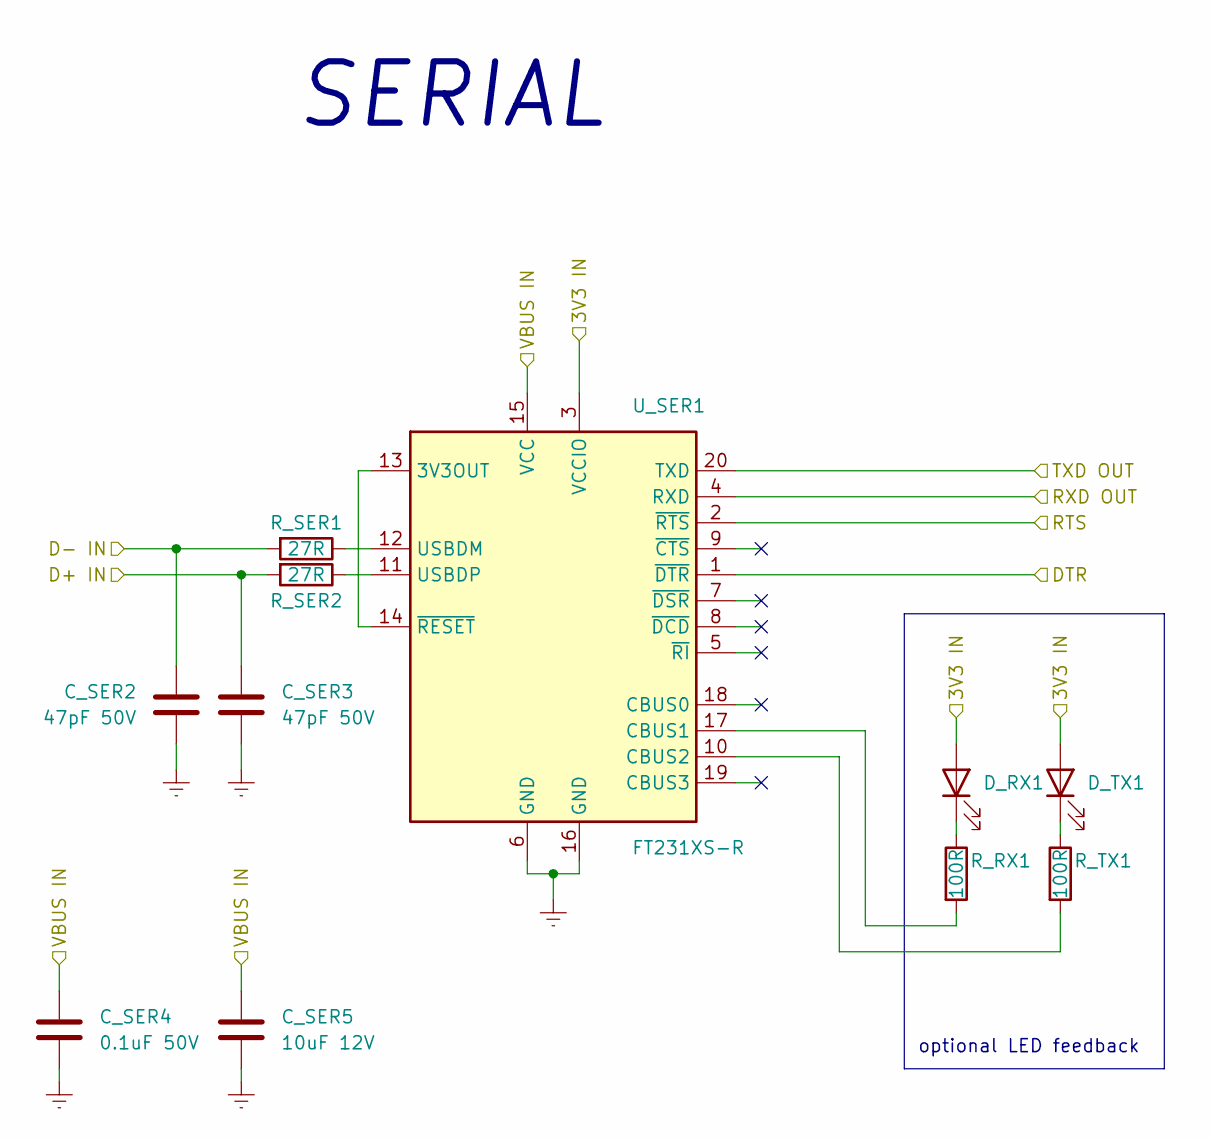
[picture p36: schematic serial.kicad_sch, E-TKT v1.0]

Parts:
C_SER2, C_SER3: 47pF 50V; C_0603_1608Metric_Pad1.08x0.95mm_HandSolder; Mouser OK
C_SER4: 0.1uF 50V; C_0603_1608Metric_Pad1.08x0.95mm_HandSolder; Mouser OK
C_SER5: 10uF 12V; C_0603_1608Metric_Pad1.08x0.95mm_HandSolder; Mouser OK
D_RX1: LED white; LED_0603_1608Metric_Pad1.05x0.95mm_HandSolder; Mouser OK
D_TX1: LED white; LED_0603_1608Metric_Pad1.05x0.95mm_HandSolder; Mouser OK
R_RX1: 100R; R_0603_1608Metric_Pad0.98x0.95mm_HandSolder; Mouser OK
R_SER1, R_SER2: 27R; R_0603_1608Metric_Pad0.98x0.95mm_HandSolder; Mouser OK
R_TX1: 100R; R_0603_1608Metric_Pad0.98x0.95mm_HandSolder; Mouser OK
U_SER1: FT231XS-R; SSOP-20_3.9x8.7mm_P0.635mm; Mouser OK

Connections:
+3.3V: D_RX1.2 (A), D_TX1.2 (A), U_SER1.3 (VCCIO); also elsewhere on the board
D+: C_SER3.2, R_SER2.2; also elsewhere on the board
D-: C_SER2.2, R_SER1.2; also elsewhere on the board
DTR: U_SER1.1 (~DTR); also elsewhere on the board
IO1 TXD: U_SER1.4 (RXD); also elsewhere on the board
IO3 RXD: U_SER1.20 (TXD); also elsewhere on the board
unnamed: D_RX1.1 (K), R_RX1.1
unnamed: D_TX1.1 (K), R_TX1.1
unnamed: R_RX1.2, U_SER1.17 (CBUS1)
unnamed: R_SER1.1, U_SER1.12 (USBDM)
unnamed: R_SER2.1, U_SER1.11 (USBDP)
unnamed: R_TX1.2, U_SER1.10 (CBUS2)
unnamed: U_SER1.13 (3V3OUT), U_SER1.14 (~RESET)
RTS: U_SER1.2 (~RTS); also elsewhere on the board
VBUS: C_SER4.1, C_SER5.2, U_SER1.15 (VCC); also elsewhere on the board

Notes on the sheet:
SERIAL
optional LED feedback

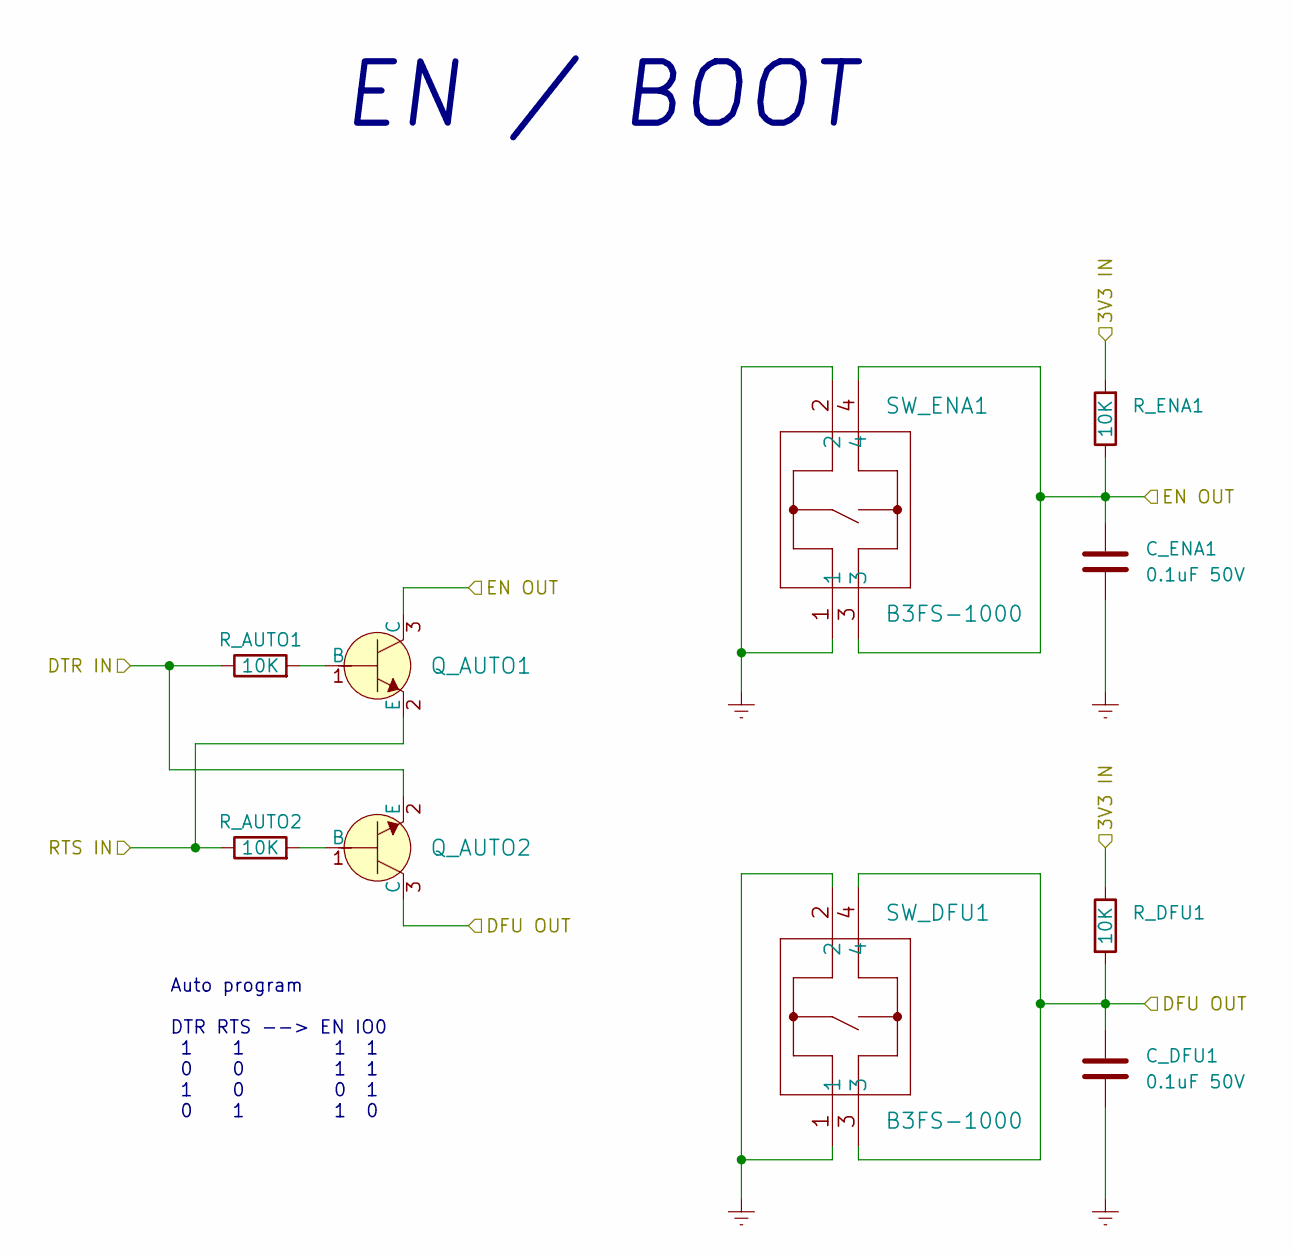
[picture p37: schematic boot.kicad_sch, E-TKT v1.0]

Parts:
C_DFU1: 0.1uF 50V; C_0603_1608Metric_Pad1.08x0.95mm_HandSolder; Mouser OK
C_ENA1: 0.1uF 50V; C_0603_1608Metric_Pad1.08x0.95mm_HandSolder; Mouser OK
Q_AUTO1, Q_AUTO2: SS8050; SOT-23_Handsoldering; Mouser OK
R_AUTO1, R_AUTO2: 10K; R_0603_1608Metric_Pad0.98x0.95mm_HandSolder; Mouser OK
R_DFU1: 10K; R_0603_1608Metric_Pad0.98x0.95mm_HandSolder; Mouser OK
R_ENA1: 10K; R_0603_1608Metric_Pad0.98x0.95mm_HandSolder; Mouser OK
SW_DFU1: B3FS-1000; Mouser OK
SW_ENA1: B3FS-1000; Mouser OK

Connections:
+3.3V: R_DFU1.1, R_ENA1.2; also elsewhere on the board
DTR: Q_AUTO2.2 (E), R_AUTO1.1; also elsewhere on the board
EN: C_ENA1.2, Q_AUTO1.3 (C), R_ENA1.1, SW_ENA1.3, SW_ENA1.4; also elsewhere on the board
IO0 DFU: C_DFU1.2, Q_AUTO2.3 (C), R_DFU1.2, SW_DFU1.3, SW_DFU1.4; also elsewhere on the board
unnamed: Q_AUTO1.1 (B), R_AUTO1.2
unnamed: Q_AUTO2.1 (B), R_AUTO2.2
RTS: Q_AUTO1.2 (E), R_AUTO2.1; also elsewhere on the board

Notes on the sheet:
Auto program DTR RTS --> EN IO0 1 1 1 1 0 0 1 1 1 0 0 1 0 1 1 0
EN / BOOT

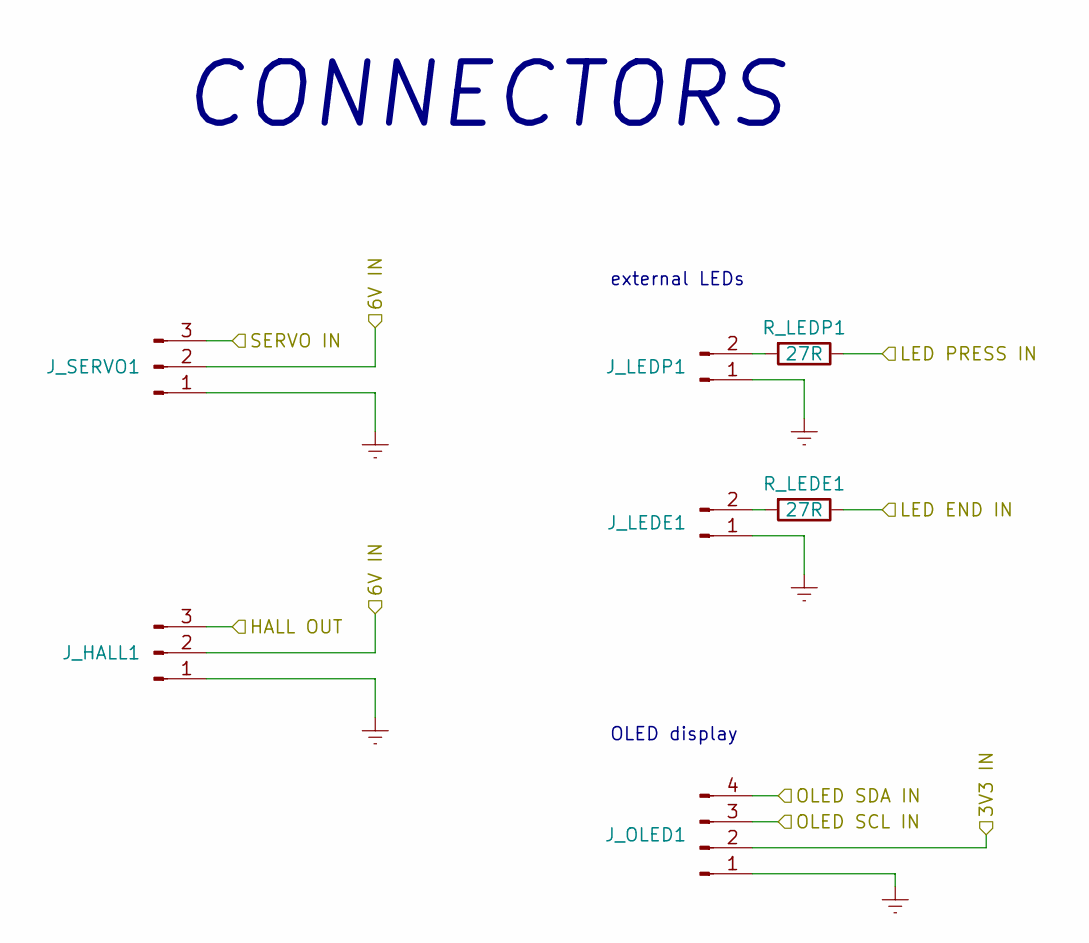
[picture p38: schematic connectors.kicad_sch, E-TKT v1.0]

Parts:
J_HALL1: Conn_01x03_Female; PinHeader_1x03_P2.54mm_Vertical; Mouser OK
J_LEDE1: Conn_01x02_Male; PinHeader_1x02_P2.54mm_Vertical; Mouser OK
J_LEDP1: Conn_01x02_Male; PinHeader_1x02_P2.54mm_Vertical; Mouser OK
J_OLED1: Conn_01x04_Male; PinHeader_1x04_P2.54mm_Vertical; Mouser OK
J_SERVO1: Conn_01x03_Male; PinHeader_1x03_P2.54mm_Vertical; Mouser OK
R_LEDE1: 27R; R_0603_1608Metric_Pad0.98x0.95mm_HandSolder; Mouser OK
R_LEDP1: 27R; R_0603_1608Metric_Pad0.98x0.95mm_HandSolder; Mouser OK

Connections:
+3.3V: J_OLED1.2; also elsewhere on the board
+6V: J_HALL1.2, J_SERVO1.2; also elsewhere on the board
HALL: J_HALL1.3; also elsewhere on the board
IO5 LED END: R_LEDE1.1; also elsewhere on the board
IO17 LED PRESS: R_LEDP1.1; also elsewhere on the board
IO21 OLED SDA: J_OLED1.4; also elsewhere on the board
IO22 OLED SCL: J_OLED1.3; also elsewhere on the board
unnamed: J_LEDE1.2, R_LEDE1.2
unnamed: J_LEDP1.2, R_LEDP1.2
SERVO: J_SERVO1.3; also elsewhere on the board

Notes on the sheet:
OLED display
CONNECTORS
external LEDs

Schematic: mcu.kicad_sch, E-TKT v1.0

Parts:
C_MCU1: 0.1uF 50V; C_0603_1608Metric_Pad1.08x0.95mm_HandSolder; Mouser OK
C_MCU2: 10uF 12V; C_0603_1608Metric_Pad1.08x0.95mm_HandSolder; Mouser OK
U_MCU1: ESP32-WROOM-32; Mouser OK

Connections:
+3.3V: C_MCU1.1, C_MCU2.2, U_MCU1.2 (VDD); also elsewhere on the board
/MCU/IO26 BUZZER OUT: U_MCU1.11 (IO26); also elsewhere on the board
EN: U_MCU1.3 (EN); also elsewhere on the board
IO0 DFU: U_MCU1.25 (IO0); also elsewhere on the board
IO1 TXD: U_MCU1.35 (TXD0/IO1); also elsewhere on the board
IO2 ULN 3: U_MCU1.24 (IO2); also elsewhere on the board
IO3 RXD: U_MCU1.34 (RXD0/IO3); also elsewhere on the board
IO4 ULN 2: U_MCU1.26 (IO4); also elsewhere on the board
IO5 LED END: U_MCU1.29 (IO5); also elsewhere on the board
IO13 WIFI RST: U_MCU1.16 (IO13); also elsewhere on the board
IO14 SERVO: U_MCU1.13 (IO14); also elsewhere on the board
IO15 ULN 1: U_MCU1.23 (IO15); also elsewhere on the board
IO16 ULN 4: U_MCU1.27 (IO16); also elsewhere on the board
IO17 LED PRESS: U_MCU1.28 (IO17); also elsewhere on the board
IO21 OLED SDA: U_MCU1.33 (IO21); also elsewhere on the board
IO22 OLED SCL: U_MCU1.36 (IO22); also elsewhere on the board
IO25 NEMA ENA: U_MCU1.10 (IO25); also elsewhere on the board
IO32 NEMA STEP: U_MCU1.8 (IO32); also elsewhere on the board
IO33 NEMA DIR: U_MCU1.9 (IO33); also elsewhere on the board
IO34 HALL: U_MCU1.6 (IO34); also elsewhere on the board

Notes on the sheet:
ESP32

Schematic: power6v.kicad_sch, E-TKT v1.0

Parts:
C_ALT6V_1: 0.33uF 50V; C_0603_1608Metric_Pad1.08x0.95mm_HandSolder; Mouser OK
C_ALT6V_2: 0.1uF 50V; C_0603_1608Metric_Pad1.08x0.95mm_HandSolder; Mouser OK
C_POW_6V_FF1: 47pF 50V; C_0603_1608Metric_Pad1.08x0.95mm_HandSolder; Mouser OK
C_POW_BST1: 0.1uF 50V; C_0603_1608Metric_Pad1.08x0.95mm_HandSolder; Mouser OK
C_POW_IN1, C_POW_IN2, C_POW_IN3: 22uF 25V; C_1210_3225Metric_Pad1.33x2.70mm_HandSolder; Mouser OK
C_POW_OUT1, C_POW_OUT2, C_POW_OUT3, C_POW_OUT4, C_POW_OUT5: 22uF 25V; C_1210_3225Metric_Pad1.33x2.70mm_HandSolder; Mouser OK
J_6v_ALT6V1, J_12v_ALT6V1: TestPoint; TestPoint_Pad_D1.5mm; Mouser OK
J_GND_ALT6V1: TestPoint; TestPoint_Pad_D1.5mm; Mouser OK
L1: SRP6060FA-100M; SRP6060FA-4R7M; Mouser OK
R_POW_FBT1: 100K; R_0603_1608Metric_Pad0.98x0.95mm_HandSolder; Mouser OK
R_POW_FFB1: 11K; R_0603_1608Metric_Pad0.98x0.95mm_HandSolder; Mouser OK
U_POW1: SOT-23-6_Handsoldering; Mouser N

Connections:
+6V: C_ALT6V_2.1, C_POW_6V_FF1.1, C_POW_OUT1.1, C_POW_OUT2.1, C_POW_OUT3.1, C_POW_OUT4.1, C_POW_OUT5.1, J_6v_ALT6V1.1, L1.2, R_POW_FBT1.2; also elsewhere on the board
+12V: C_ALT6V_1.2, C_POW_IN1.1, C_POW_IN2.1, C_POW_IN3.1, J_12v_ALT6V1.1, U_POW1.3 (VIN); also elsewhere on the board
unnamed: C_POW_6V_FF1.2, R_POW_FBT1.1, R_POW_FFB1.2, U_POW1.4 (FB)
unnamed: C_POW_BST1.1, U_POW1.6 (BOOT)
unnamed: C_POW_BST1.2, L1.1, U_POW1.2 (SW)

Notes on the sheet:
alternative 6V output: 7806 linear regulator
6V POWER BUCK CONVERTER

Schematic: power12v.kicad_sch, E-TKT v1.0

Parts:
D_POW2: LED white; LED_0603_1608Metric_Pad1.05x0.95mm_HandSolder; Mouser OK
J_POW1: Barrel_Jack_Switch; BarrelJack_GCT_DCJ200-10-A_Horizontal; Mouser OK
R_POW6: 5K1; R_0603_1608Metric_Pad0.98x0.95mm_HandSolder; Mouser OK

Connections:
+12V: J_POW1.1, R_POW6.1; also elsewhere on the board
unnamed: D_POW2.2 (A), R_POW6.2

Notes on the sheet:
optional LED feedback
12V POWER + LATCH SWITCH

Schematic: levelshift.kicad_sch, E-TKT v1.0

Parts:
D_HALL1: LED white; LED_0603_1608Metric_Pad1.05x0.95mm_HandSolder; Mouser OK
D_SERVO1: LED white; LED_0603_1608Metric_Pad1.05x0.95mm_HandSolder; Mouser OK
Q_HALL1: BSS138LT3G; SOT-23_Handsoldering; Mouser OK
Q_SERVO1: BSS138LT3G; SOT-23_Handsoldering; Mouser OK
R_HALL1, R_HALL2: 10K; R_0603_1608Metric_Pad0.98x0.95mm_HandSolder; Mouser OK
R_HALL3: 100R; R_0603_1608Metric_Pad0.98x0.95mm_HandSolder; Mouser OK
R_SERVO1, R_SERVO2: 10K; R_0603_1608Metric_Pad0.98x0.95mm_HandSolder; Mouser OK
R_SERVO3: 100R; R_0603_1608Metric_Pad0.98x0.95mm_HandSolder; Mouser OK

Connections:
+3.3V: D_HALL1.2 (A), D_SERVO1.2 (A), Q_HALL1.1 (G), Q_SERVO1.1 (G), R_HALL2.2, R_SERVO2.2; also elsewhere on the board
+6V: R_HALL1.2, R_SERVO1.2; also elsewhere on the board
HALL: Q_HALL1.3 (D), R_HALL1.1; also elsewhere on the board
IO14 SERVO: Q_SERVO1.2 (S), R_SERVO2.1, R_SERVO3.1; also elsewhere on the board
IO34 HALL: Q_HALL1.2 (S), R_HALL2.1, R_HALL3.1; also elsewhere on the board
unnamed: D_HALL1.1 (K), R_HALL3.2
unnamed: D_SERVO1.1 (K), R_SERVO3.2
SERVO: Q_SERVO1.3 (D), R_SERVO1.1; also elsewhere on the board

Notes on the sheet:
optional LED feedback
LEVEL SHIFT

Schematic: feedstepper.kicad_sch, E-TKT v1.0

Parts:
C_STP1: 10uF 12V; C_0603_1608Metric_Pad1.08x0.95mm_HandSolder; Mouser OK
D_STP1, D_STP2, D_STP3, D_STP4: LED white; LED_0603_1608Metric_Pad1.05x0.95mm_HandSolder; Mouser OK
J_28byj-48-12v_1: Conn_01x05_Male; PinHeader_1x05_P2.54mm_Vertical; Mouser OK
R_STP1, R_STP2, R_STP3, R_STP4: 5K1; R_0603_1608Metric_Pad0.98x0.95mm_HandSolder; Mouser OK
U_STP1: ULN2003; SOIC-16_3.9x9.9mm_P1.27mm; Mouser OK

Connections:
+12V: C_STP1.2, J_28byj-48-12v_1.1, R_STP1.1, R_STP2.1, R_STP3.1, R_STP4.1, U_STP1.9 (COM); also elsewhere on the board
IO2 ULN 3: U_STP1.3 (I3); also elsewhere on the board
IO4 ULN 2: U_STP1.2 (I2); also elsewhere on the board
IO15 ULN 1: U_STP1.1 (I1); also elsewhere on the board
IO16 ULN 4: U_STP1.4 (I4); also elsewhere on the board
unnamed: D_STP1.1 (K), J_28byj-48-12v_1.2, U_STP1.16 (O1)
unnamed: D_STP1.2 (A), R_STP1.2
unnamed: D_STP2.1 (K), J_28byj-48-12v_1.3, U_STP1.15 (O2)
unnamed: D_STP2.2 (A), R_STP2.2
unnamed: D_STP3.1 (K), J_28byj-48-12v_1.4, U_STP1.14 (O3)
unnamed: D_STP3.2 (A), R_STP3.2
unnamed: D_STP4.1 (K), J_28byj-48-12v_1.5, U_STP1.13 (O4)
unnamed: D_STP4.2 (A), R_STP4.2

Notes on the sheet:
optional LED feedback
STEPPER FEED

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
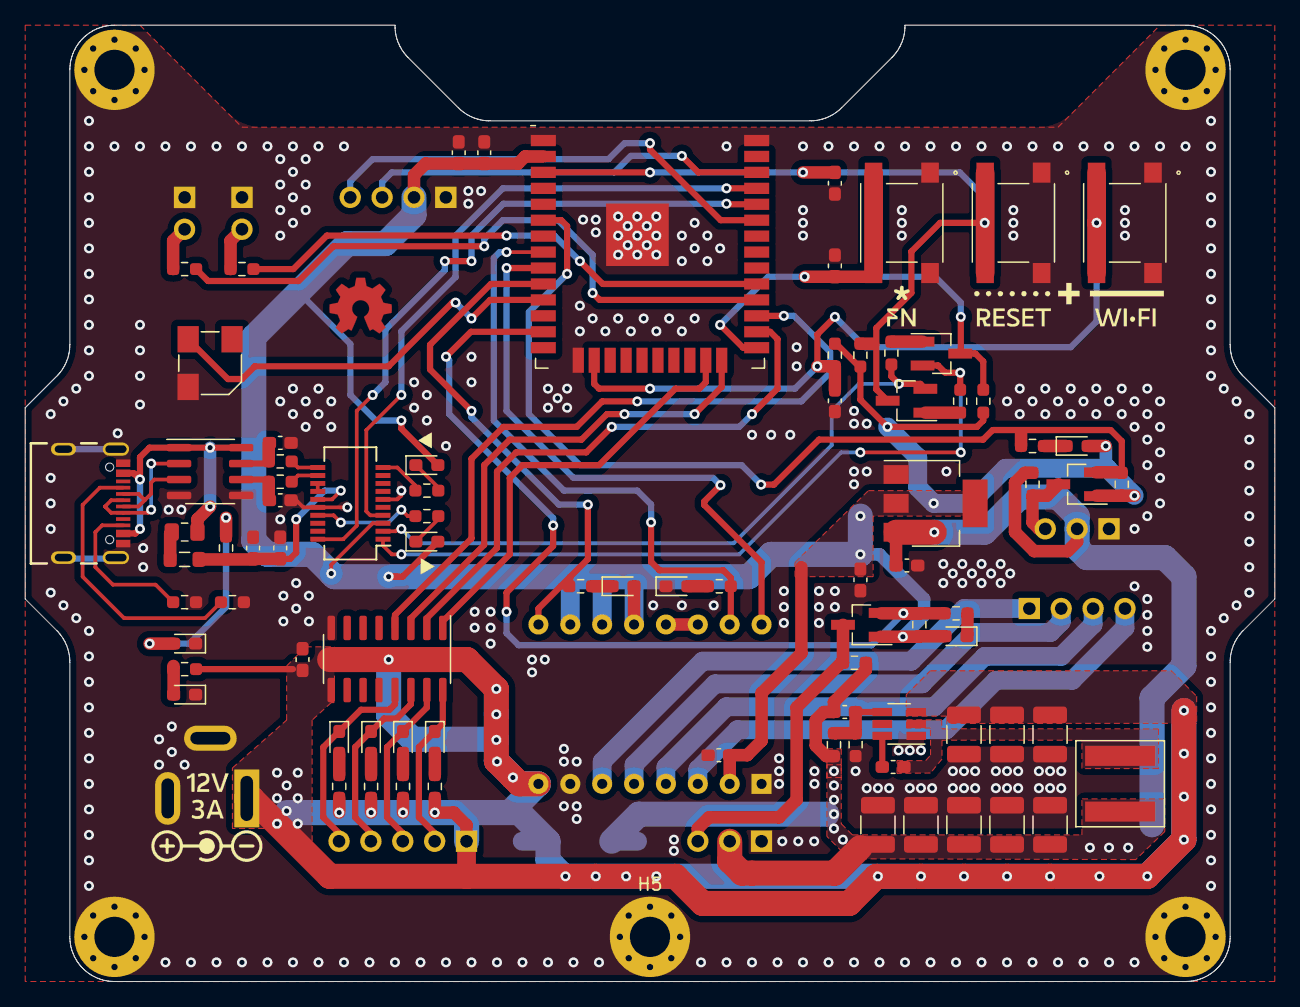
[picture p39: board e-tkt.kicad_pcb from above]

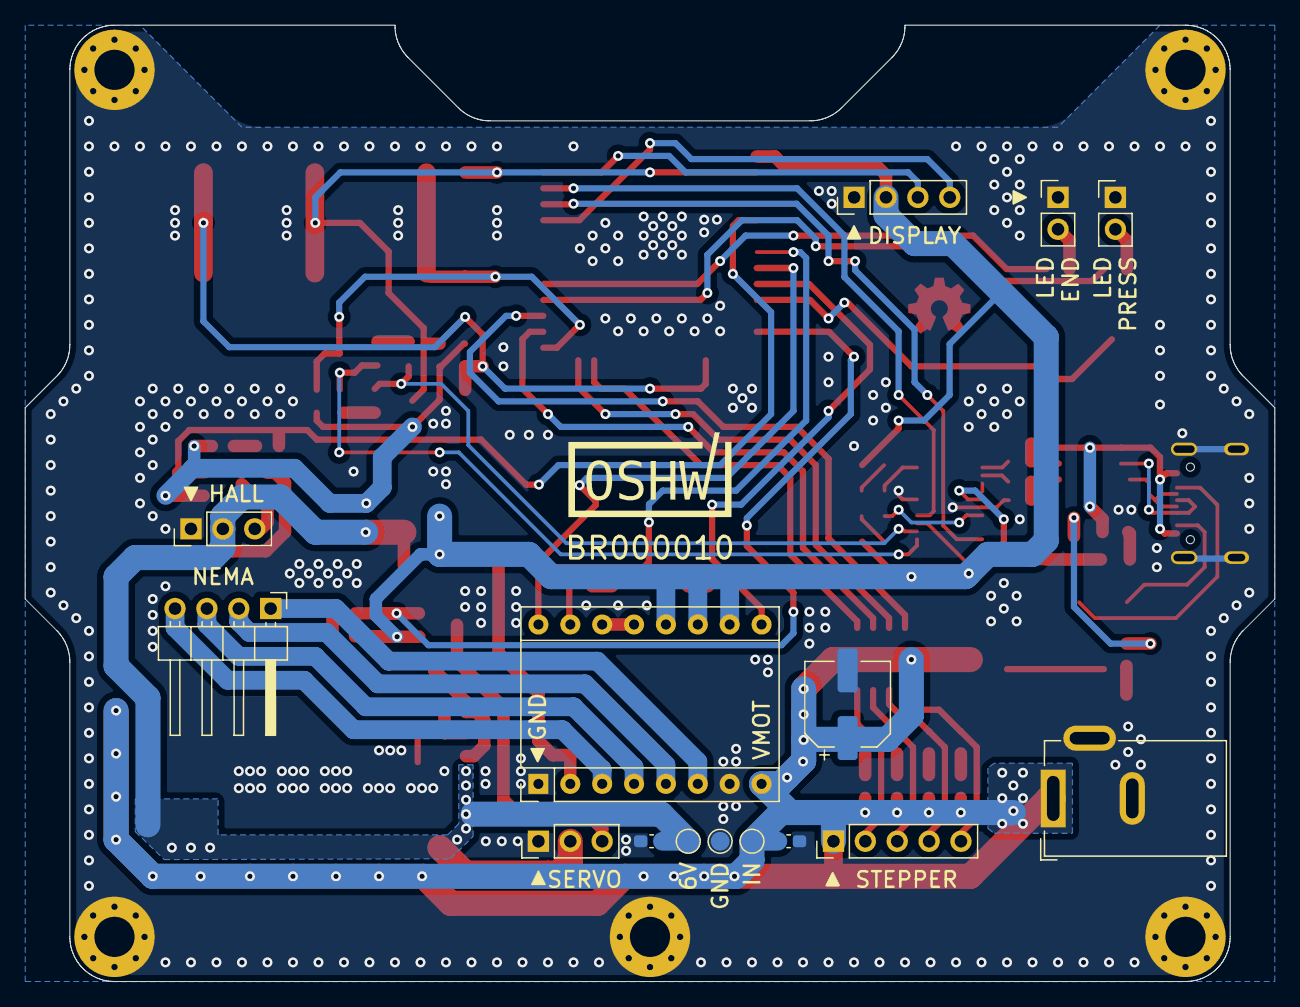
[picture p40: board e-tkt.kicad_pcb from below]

Board: 4 copper layers, 99.6 x 76.2 mm, 102 parts (15 on the bottom side), 69 nets.

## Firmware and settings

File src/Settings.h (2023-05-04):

#pragma once

#include <Arduino.h>
#include <preferences.h>

#include <tuple>

#include "Configuration.h"
#include "Logger.h"

#define DEFAULT_ALIGN_FACTOR 5  // 1 to 9, 5 is the mid value
#define DEFAULT_FORCE_FACTOR 1  // 1 to 9

/**
 * @brief Stores and retrieves settings from EEPROM using the
 * preference library.
 */
class Settings {
 private:
  Logger* logger;
  Preferences* preferences = new Preferences();
  uint alignFactor = 0;
  uint forceFactor = 0;

 public:
  Settings(Logger* logger);
  ~Settings();

  /**
   * @brief Initializes the settings object by loading the settings from EEPROM.
   */
  void initialize();

  /**
   * @brief Returns the current alginment calbration value
   */
  uint32_t getAlignFactor();

  /**
   * @brief Returns the current force calibration value
   */
  uint32_t getForceFactor();

  /**
   * @brief Saves the given alignment and force calibration values to EEPROM.
   */
  void save(uint32_t newAlignFactor, uint32_t newForceFactor);
};

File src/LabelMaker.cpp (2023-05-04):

// MIT License

// Copyright (c) 2022 Andrei Speridião

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
//
// for more information, please visit https://github.com/andreisperid/E-TKT
//

// vvvvvvvvvvvvvvvvvvvvvvvvvvvvvvvvvvvvvvvvvvvvvvvvvvvvvvvvvvvvvvvvvvvvvvvvvv
//
// IMPORTANT: do not forget to upload the files in "data" folder using SPIFFS
//
// ^^^^^^^^^^^^^^^^^^^^^^^^^^^^^^^^^^^^^^^^^^^^^^^^^^^^^^^^^^^^^^^^^^^^^^^^^^

#include <Arduino.h>

#include "DaisyWheel.h"
#include "Characters.h"
#include "Configuration.h"
#include "Display.h"
#include "ETKT.h"
#include "Feeder.h"
#include "HallSwitch.h"
#include "Light.h"
#include "Logger.h"
#include "Network.h"
#include "Press.h"
#include "Settings.h"
#include "Sound.h"
#include "Utility.h"

Logger* logger = new Logger();
Characters* characters = new Characters();
Sound* sound = new Sound(characters);
Display* display = new Display(sound, characters);
Settings* settings = new Settings(logger);
Light* ledFinish = new Light(FINISH_LED_PIN);
Light* ledChar = new Light(CHARACTER_LED_PIN);
Press* press = new Press(logger, SERVO_PIN, ledChar);
HallSwitch* hall = new HallSwitch(logger, HALL_PIN);
DaisyWheel* daisywheel = new DaisyWheel(logger, hall, characters, settings);
Feeder* feeder = new Feeder(logger);
ETKT* etkt = new ETKT(logger, settings, characters, display, daisywheel, hall,
                      feeder, press, sound, ledFinish, ledChar);
Network* network = new Network(logger, display, etkt, WIFI_RESET_PIN);

void setup() {
  // Initialize hardware
  etkt->initialize();

  // Play the splash screen
  display->playSplashScreen();

  // Start WiFi, network.
  network->initialize();

  // Display the ready "idle" screen.
  display->renderIdle();
}

void loop() { etkt->loop(); }

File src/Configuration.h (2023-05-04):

#pragma once

#include <Arduino.h>

/**
 * Basic Configuration
 *
 * Depending on the hardware you've used to build your E-TKT, you might need to
 * enable some of these constants to get the hardware into a working state
 */

/**
 * If your hall sensor has inverted logic (eg active LOW and neutral HIGH)
 * uncomment this #define to invert the logic checking it. If you're affected by
 * this then you'll see the character daisy wheel move forward slightly and then
 * stop when the E-TKT starts up instead of moving to the "J" position.
 *
 * For instance, invert if using a "3144" hall sensor but don't invert if using
 * a "44E 402" hall sensor. If you're not sure if you need this, try it both
 * ways and see which one works.
 */
#define INVERT_HALL_SENSOR_LOGIC false

/**
 * If your feed motor moves in the wrong direction by default, uncomment the
 * define below to reverse it. It should be obvious if this is happening since
 * the tape gets fed in the wrong direction.
 */
#define REVERSE_FEED_STEPPER_DIRECTION false

/**
 * Speed and acceleration of the stepper motor that feeds the label tape,
 * measured in steps/s and steps/s^2. Use lower values if you find that the
 * printer doesn't consistently feed the correct length of tape between letters.
 * For calibrating these values the same advice about the character stepper
 * motor above applies. 4076 steps is one full revolution of the motor.
 */
#define FEED_STEPPER_MAX_SPEED 1000000
#define FEED_STEPPER_MAX_ACCELERATION 1000

/**
 * Speed and acceleration of the stepper motor that rotates the character
 * daisy wheel, measured in steps/s and steps/s^2. Use lower values if you find
 * that the printer sometimes prints the wrong letter.  Any value above zero is
 * ok but lower values will slow down printing, if you're having trouble start
 * by halving them and move up from there.  The speed you can reliably achieve
 * depends on the quality of the motor, how much current you've set it up to
 * use, and how fast the ESP-32 can talk with it. 1600 steps is a full
 * revolution of the daisy wheel.
 */
#define CHARACTER_STEPPER_MAX_SPEED 320000
#define CHARACTER_STEPPER_MAX_ACCELERATION 16000

/**
 * Debugging
 *
 * Alter these to enable/disable individual parts of the hardware while
 * troubleshooting.
 */
#define ENABLE_SOUND true
#define ENABLE_FEED true
#define ENABLE_CUT true
#define ENABLE_PRESS true
#define ENABLE_DAISYWHEEL true

/**
 * Development
 *
 * Developers of the firmware may find it useful to turn on these features
 */
#define ENABLE_SERIAL false  // Enables serial output
#define ENABLE_OTA false     // Enables OTA updates at http://e-tkt.local/update
#define DEBUG_WIFI false     // Enables WiFi debugging

/**
 * Hardware Pins
 */
#define HALL_PIN 34        // hall sensor
#define WIFI_RESET_PIN 13  // tact switch
#define SERVO_PIN 14       // Press servo
#define CHARACTER_LED_PIN 17
#define FINISH_LED_PIN 5
#define PIN_STEPPER_CHAR_STEP 32
#define PIN_STEPPER_CHAR_DIR 33
#define PIN_STEPPER_CHAR_ENABLE 25
#define BUZZER_PIN 26

/**
 * Physical Characteristics
 *
 * Physical characteristics of the printer.  These are used to calculate the
 * number of steps required to move and are unlikely to ever need to be changed.
 */

#define CHAR_MICROSTEPS 16
#define CHAR_STEP_COUNT 200
// depending on the hall sensor positioning, the variable below makes sure the
// initial calibration is within tolerance use a value between -1.0 and 1.0 to
// make it roughly align during assembly
#define ASSEMBLY_CALIBRATION_ALIGN 0.5f
#define CHAR_HOME_POSITION 21

// depending on servo characteristics and P_press assembling process, the
// pressing angle might not be so precise and the value below compensates it use
// a value between 0 and 20 to make sure the press is barely touching the daisy
// wheel on test align
#define ASSEMBLY_CALIBRATION_FORCE 15
#define MICROSTEPS_FEED 8
#define FEED_MOTOR_STEPS_PER_REVOLUTION 4076
#define HALL_SENSOR_THRESHOLD 128  // between 0 and 4096

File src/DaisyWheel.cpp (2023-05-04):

#include "DaisyWheel.h"

#include <AccelStepper.h>

#include "Arduino.h"
#include "Characters.h"
#include "Configuration.h"
#include "HallSwitch.h"
#include "Logger.h"
#include "Settings.h"

DaisyWheel::DaisyWheel(Logger* logger, HallSwitch* hall, Characters* characters,
                   Settings* settings) {
  this->logger = logger;
  this->hall = hall;
  this->characters = characters;
  this->settings = settings;
  this->stepper = new AccelStepper(AccelStepper::DRIVER, PIN_STEPPER_CHAR_STEP,
                                   PIN_STEPPER_CHAR_DIR);
}

DaisyWheel::~DaisyWheel() { delete stepper; }

void DaisyWheel::initialize() {
  this->stepsPerChar = (float)this->stepsPerRevolution /
                       this->characters->getWheelCharacterCount();
  digitalWrite(PIN_STEPPER_CHAR_ENABLE, HIGH);
  this->stepper->setMaxSpeed(CHARACTER_STEPPER_MAX_SPEED);
  this->stepper->setAcceleration(CHARACTER_STEPPER_MAX_ACCELERATION);
  this->stepper->setPinsInverted(true, false, true);
  this->stepper->setEnablePin(PIN_STEPPER_CHAR_ENABLE);
  this->home(this->settings->getAlignFactor());  // initial home for reference
  this->deenergize();
}

void DaisyWheel::home(int align) {
  this->stepper->enableOutputs();
  // runs the char stepper clockwise until triggering the hall sensor, then call
  // it home at char 21
  auto a = (align - 5.0f) / 10.0f;

  logger->log(String("Homing with align: ") + align + " and a: " + a);

  // Check to see if the hall sensor on the stepper is already trigerred
  // and if so, move it a little bit to get the sensor into an un-trigerred
  // position.
  if (this->hall->triggered()) {
    long position = -this->stepsPerChar * 4;
    logger->log(String("Moving to position: ") + position +
                " because the hall sensor is already triggered.");
    this->stepper->runToNewPosition(-this->stepsPerChar * 4);
    this->stepper->run();
  }

  // TODO: Change the above to only move as long as the hall sensor is
  // triggerred, which could save a little time while printing.

  // Move the daisy wheel until the hall sensor triggers, and then treat wherever
  // that is as the new home position.
  this->stepper->move(-this->stepsPerRevolution * 1.5f);
  auto hallState = hall->triggered();
  while (!hallState) {
    this->stepper->run();
    // TODO: less intrusive way to avoid triggering watchdog?
    delayMicroseconds(100);

    hallState = hall->triggered();
  }
  // TODO: Add a failure path for if the stepper moved a full rotation without
  // trigerring the sensor, inidcating that something is wrong with the
  // hardware.
  this->stepper->setCurrentPosition(0);

  this->stepper->runToNewPosition(-stepsPerChar + (stepsPerChar * a) +
                                  (ASSEMBLY_CALIBRATION_ALIGN * stepsPerChar));
  this->stepper->run();
  this->stepper->setCurrentPosition(0);
  this->currentChar = CHAR_HOME_POSITION;

  delay(100);
}

bool DaisyWheel::move(String c, int alignFactor) {
  if (!ENABLE_DAISYWHEEL) {
    delay(500);
    return true;
  }

  // reaches out for a specific character
  logger->log(String("Moving to character ") + c);
  this->stepper->enableOutputs();
  auto charIndex = this->characters->getCharacterIndex(c);
  if (charIndex < 0) {
    // Invalid character
    return false;
  }
  if (charIndex == this->currentChar) {
    // No need to move, we're already there.
    logger->log("Already in position");
    return true;
  }

  // calls home everytime to avoid accumulating errors
  this->home(alignFactor);

  auto charDelta = charIndex - this->currentChar;
  logger->log(String("New character index is ") + charIndex +
              " and character delta is " + charDelta);
  // matches the character to the list and gets delta steps from home
  while (charDelta < 0) {
    charDelta += this->characters->getWheelCharacterCount();
  }

  if (charDelta == 0) {
    // No need to move, we're already there
    logger->log("Already in position");
    return true;
  }

  // runs char stepper clockwise to reach the target position
  long position = -this->stepsPerChar * charDelta;
  logger->log(String("Moving ") + charDelta + " characters to position " +
              position);
  this->stepper->runToNewPosition(position);
  this->currentChar = charIndex;

  delay(25);
  return true;
}

void DaisyWheel::deenergize() {
  this->stepper->disableOutputs();

  // Disabling the motors loses position information, so we need to reset it.
  this->currentChar = -1;
}

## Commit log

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2021-10-12 fixed spaces after string
    [LabelMaker.cpp]
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2022-05-26 3d print files
    [B_wall.stl, C_wall_track.stl, D_pillar_1.stl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]
2022-05-26 fixed name on 3d printed file
2022-05-26 renamed 3dprint folder
    [B_wall.stl, C_wall_track.stl, D_pillar_1.stl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]
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2022-06-01 folder arrangement for 3d and electronic files
    [B_wall.stl, C_wall_track.stl, D_pillar_1.stl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]
2022-06-01 fixed gitignore and added instructions on code
    [LabelMaker.cpp]
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2022-06-01 removed stl folder
    [B_wall.stl, C_wall_track.stl, D_pillar_1.stl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]
2022-06-01 added folder with oriented stl
    [B_wall.stl, C_wall_track.stl, D_pillar_1.stl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]
2022-06-01 correct stl files
    [B_wall.stl, C_wall_track.stl, D_pillar_1.stl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]
2022-06-01 fixed stl name
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2022-06-22 schematics draft
    [e-tkt.kicad_pcb, e-tkt.kicad_sch]
2022-06-24 organized and adjusted schematics
    [e-tkt.kicad_sch]
2022-06-24 pcb draft
    [e-tkt.kicad_pcb]
2022-06-27 pcb draft with esp32-s3
    [e-tkt.kicad_pcb, e-tkt_esp32.kicad_pcb, e-tkt_esp32.kicad_sch]
2022-06-30 improved pcb design, with parts in stock
    [e-tkt.kicad_pcb, e-tkt.kicad_sch]
2022-07-05 needs revision
    [e-tkt.kicad_pcb, e-tkt.kicad_sch]
2022-07-07 tvs diode, ground plane, schematics layout
    [e-tkt.kicad_pcb, e-tkt.kicad_sch]
2022-07-07 fixed esp footprint/symbol, plus vias and holes
    [e-tkt.kicad_pcb, e-tkt.kicad_sch]
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2022-07-09 bigger board, switch back to esp32
    [e-tkt.kicad_pcb, e-tkt.kicad_sch, e-tkt_small.kicad_pcb]
2022-07-10 board silhouette and ftdi
    [e-tkt.kicad_pcb, e-tkt.kicad_sch]
2022-07-10 board dimensions, taller
    [e-tkt.kicad_pcb, e-tkt.kicad_sch]
2022-07-11 improved decouple caps position, routing
    [e-tkt.kicad_pcb, e-tkt.kicad_sch]
2022-07-13 led resistors, better pcb layout, omron tact
    [e-tkt.kicad_sch]
2022-07-13 rev1 schematics export
    [e-tkt.kicad_sch]
2022-07-15 ftdi revision, removed usb vcc jumper
    [drafts.kicad_sch, e-tkt.kicad_sch]
2022-07-16 bucket 6v and latch power
    [e-tkt.kicad_pcb, e-tkt.kicad_sch]
2022-07-19 added vias, revised parts, fixed schematic
    [6vpower.kicad_sch, e-tkt.kicad_pcb, e-tkt.kicad_sch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]
2022-07-20 visual identity on silk and exposed copper layers
    [e-tkt.kicad_pcb, e-tkt.kicad_sch]
2022-07-20 deleted backups
    [e-tkt_esp32.kicad_pcb, e-tkt_esp32.kicad_sch]
2022-07-20 hierarchical sheets and overall organization
    [6vpower.kicad_sch, boot.kicad_sch, charstepper.kicad_sch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]
2022-07-20 added buzzer
    [boot.kicad_sch, charstepper.kicad_sch, connectors.kicad_sch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]
2022-07-20 external flashing header
    [boot.kicad_sch, e-tkt.kicad_sch, extflashing.kicad_sch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]
2022-07-21 6v and power latch backup
    [e-tkt.kicad_sch, power12v.kicad_sch, power6v.kicad_sch]
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2022-07-21 revised IC packages, pins and footprints
    [boot.kicad_sch, charstepper.kicad_sch, e-tkt.kicad_sch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]
2022-07-22 better buck layout and final revision
    [connectors.kicad_sch, e-tkt.kicad_sch]
2022-07-22 schematics footer and export
    [boot.kicad_sch, charstepper.kicad_sch, connectors.kicad_sch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]
2022-07-22 fixed 3d pcb export folders
2022-09-02 buzzer with sound features
    [LabelMaker.cpp]
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2022-09-20 revised pcb: direct power, leds, ftdi w/o 3v3
    [C_wall_track_2.stl, P_press.stl, _rc_C_wall_track.stl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]
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2022-09-23 fn label on silkscreen
    [e-tkt.kicad_pcb]
2022-09-23 fixed silk layer
    [e-tkt.kicad_pcb]
2022-09-23 pcb v1 to production
    [e-tkt.kicad_pcb]
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2022-09-28 v1.0 3d printed files
    [C_wall_track.stl, C_wall_track_2.stl, D_pillar.stl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]
2022-09-28 led resistor revision, b.o.m. and pcb anotation
    [boot.kicad_sch, charstepper.kicad_sch, connectors.kicad_sch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]
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2022-09-29 buzzer on pin 26
    [LabelMaker.cpp]
2022-09-29 schematics and pcb cleanup
    [boot.kicad_sch, charstepper.kicad_sch, connectors.kicad_sch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]
2022-10-05 fixed web app button states and layout
    [LabelMaker.cpp]
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2022-10-07 alternative file for P_press 3d print
    [P_press_1mmleft.stl]
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2022-10-14 buzzer pin on new pcb
    [LabelMaker.cpp]
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2022-10-17 fixed wrong hall header on pcb
    [e-tkt.kicad_pcb]
2022-10-18 fixed hall header on pcb
    [connectors.kicad_sch, e-tkt.kicad_pcb, e-tkt.kicad_sch]
2022-10-18 removed old electronic files
    [e-tkt.csv]
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2023-02-08 fixed 99% progress when beginning printing
    [LabelMaker.cpp]
2023-02-17 Note the prevChar is changed during homing
    Otherwise the printer can print the wrong character at the start of a print
    [LabelMaker.cpp]
2023-03-20 fixes 'char' to 'const char*' convertion error
    [LabelMaker.cpp]
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2023-04-12 Update bom.md
    Added proper spec names for fasteners and replaced 2 rotted links with generic search links
2023-04-13 Update bom.md
    Replaced rotted links with new ones or search links (the servo is currently only available as multiple).
    Also added an example for the power brick.
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2023-04-19 add separated 3D STEP files, by layer
    [E-TKT_024-electronic_LED_DIP-2x5x7mm.stp, E-TKT_024-electronic_external models_28BYJ-48 - 5V by Pablo Galarce.stp, E-TKT_024-electronic_external models_MG-995 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]
2023-04-19 updated step files, m3x16 side screws
    [E-TKT_024-electronic_LED_DIP-2x5x7mm.stp, E-TKT_024-electronic_external models_28BYJ-48 - 5V by Pablo Galarce.stp, E-TKT_024-electronic_external models_MG-995 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]
2023-04-19 updated stl files, m3x16 side screws
    [K_top_screenholder.stl]
2023-04-20 added first version of custom pressWheel
    [pressWheel.scad, pressWheel_42_ABC123_test.stl, pressWheel_42_ABC123_test_Top.stl]
2023-04-24 improved custom wheel test
    [pressWheel.scad, pressWheel_42_ABC123_test.stl, pressWheel_42_ABC123_test_Top.stl]
2023-04-24 adjusted custom wheel parameters
    [pressWheel.scad]
2023-04-25 added a section cut option to help with tuning
    [pressWheel.scad]
2023-04-25 closed the small gaps at bottom disc center
    [pressWheel.scad]
2023-04-25 embHght represents the char height again
    [pressWheel.scad]
2023-04-25 introduced option to show the positives in the topwheel to better see spacing spacings are now selectable for XY and Z separately
    [pressWheel.scad]
2023-04-25 added option to render labels to the top disc
    [pressWheel.scad]
2023-04-25 started experimenting with fonts
    [pressWheel.scad]
2023-04-25 created module for 16segment display
    [pressWheel.scad]
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2023-04-25 Update pressWheel.scad
    user can now select to create a 16-segment inspired wheel. Letters and numbers needs to be combined by multiple presses without feeding the tape.
    [pressWheel.scad]
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2023-04-29 Revert some accidentally submitted #define changes
    [LabelMaker.cpp]
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2023-05-02 Break out firmware into multiple classes.
    [Configuration.h]
2023-05-03 Fix progress reporting (webapp and firmware)
    [ETKT.cpp]
2023-05-03 Properly handle printer busy error
    [ETKT.cpp]
2023-05-03 rename from Carousel to DaisyWheel
    [Configuration.h, pressWheel.scad]
2023-05-04 fixes the LEDs behavior

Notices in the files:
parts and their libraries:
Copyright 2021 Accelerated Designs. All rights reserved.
